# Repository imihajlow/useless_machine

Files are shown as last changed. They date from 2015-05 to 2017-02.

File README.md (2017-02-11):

# Useless machine

This project is an attempt to design a useless machine (the one that does nothing but turing off the switch) from scratch.
The reductor gears are designed to be 3d-printed.
The low-power controller can be reused for other small applications: it provides some GPIO pins, UART, and bidirectional motor driver.
The controller's power consumption is low enough to sustain on a CR2032 battery for more than 1.5 years in standby mode.

* mechanics/ - AutoCAD drawings of the mechanical part of the machine. This folder also contains the belt length calculation script.
* controller/ - the electronic part. Schematic drawing, PCB layout and gerber files for production.
* firmware/ - firmware for the controller. You need SDCC (http://sdcc.sourceforge.net) to compile.

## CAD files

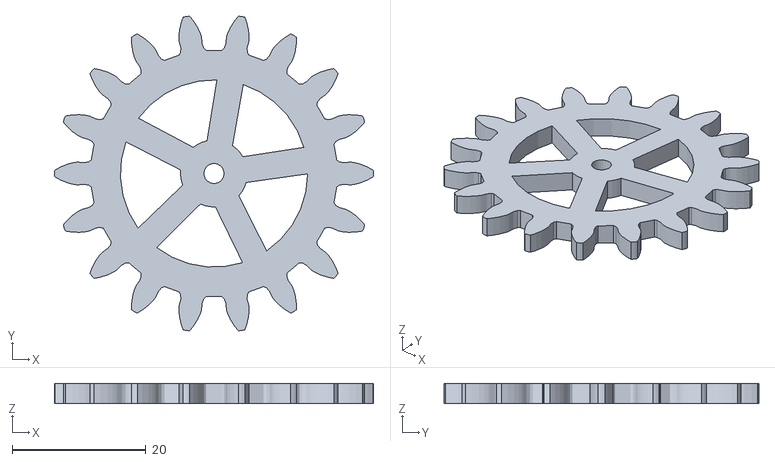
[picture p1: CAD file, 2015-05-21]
mechanics/3.stl
47.7 x 47.1 x 3.00

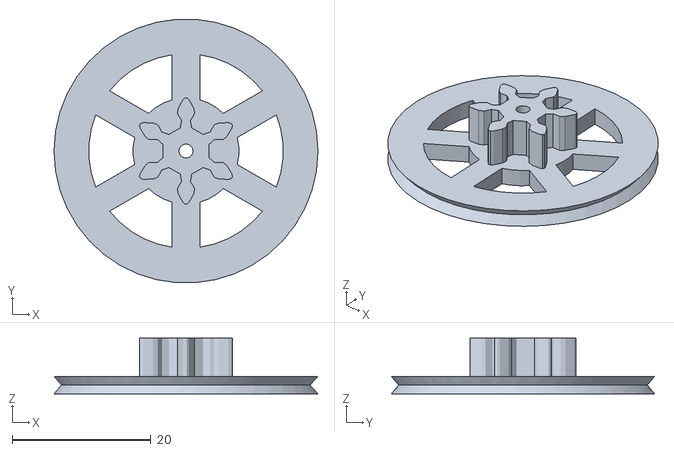
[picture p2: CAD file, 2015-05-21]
mechanics/1.stl
38.0 x 37.9 x 8.00

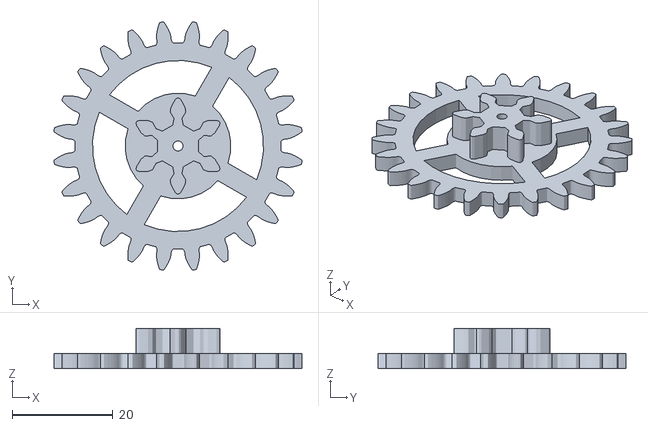
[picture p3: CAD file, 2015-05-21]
mechanics/2.stl
49.3 x 49.3 x 8.00

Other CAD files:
mechanics/layout-v2.dwg
mechanics/ver2.dwg
mechanics/machine.dwg

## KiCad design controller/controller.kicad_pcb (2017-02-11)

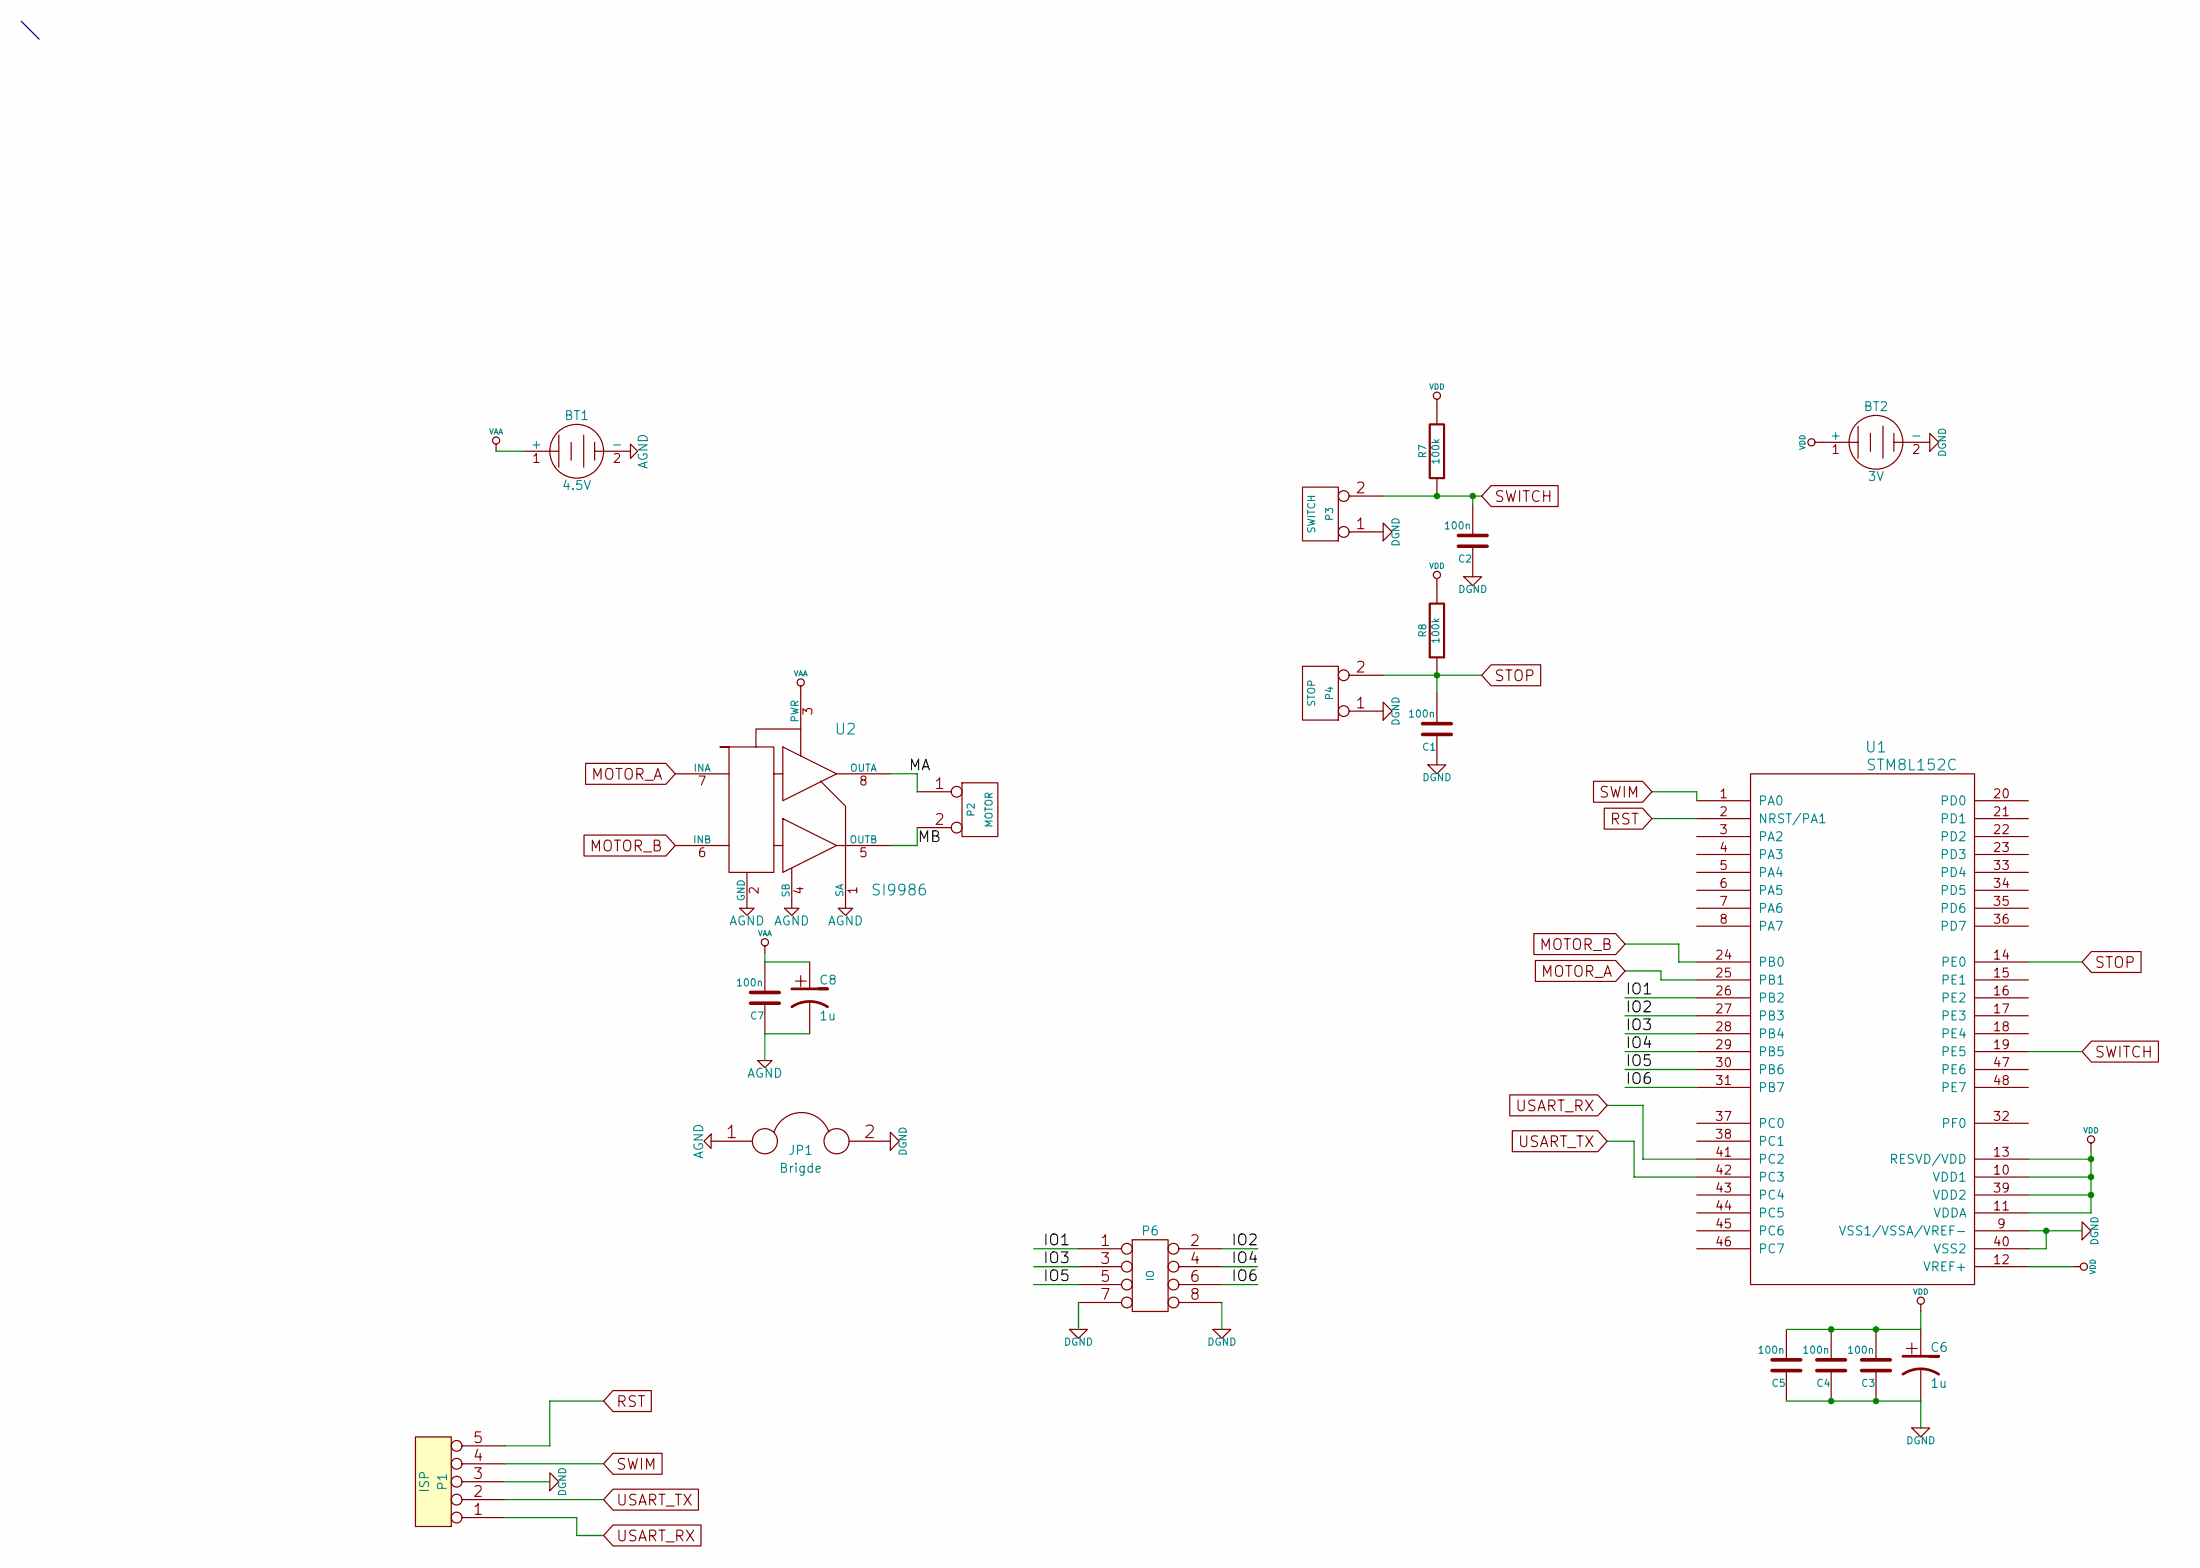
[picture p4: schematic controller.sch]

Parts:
BT1: 4.5V
BT2: 3V
C1, C2, C3, C4, C5, C7: 100n
C6, C8: 1u
JP1: Brigde
P1: ISP
P2: MOTOR
P3: SWITCH
P4: STOP
P6: IO
R7, R8: 100k
U1: STM8L152C
U2: SI9986

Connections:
/IO1: P6.1, U1.26 (PB2)
/IO2: P6.2, U1.27 (PB3)
/IO3: P6.3, U1.28 (PB4)
/IO4: P6.4, U1.29 (PB5)
/IO5: P6.5, U1.30 (PB6)
/IO6: P6.6, U1.31 (PB7)
/MA: P2.1, U2.8 (OUTA)
/MB: P2.2 (PM), U2.5 (OUTB)
AGND: BT1.2 (-), C7.1, C8.2, JP1.1, U2.1 (SA), U2.2 (GND), U2.4 (SB)
DGND: BT2.2 (-), C1.1, C2.1, C3.1, C4.1, C5.1, C6.2, JP1.2, P1.3, P3.1, P4.1, P6.7, P6.8, U1.9 (VSS1/VSSA/VREF-), U1.40 (VSS2)
MOTOR_A: U1.25 (PB1), U2.7 (INA)
MOTOR_B: U1.24 (PB0), U2.6 (INB)
RST: P1.5, U1.2 (NRST/PA1)
STOP: C1.2, P4.2 (PM), R8.1, U1.14 (PE0)
SWIM: P1.4, U1.1 (PA0)
SWITCH: C2.2, P3.2 (PM), R7.1, U1.19 (PE5)
USART_RX: P1.1, U1.41 (PC2)
USART_TX: P1.2, U1.42 (PC3)
VAA: BT1.1 (+), C7.2, C8.1, U2.3 (PWR)
VDD: BT2.1 (+), C3.2, C4.2, C5.2, C6.1, R7.2, R8.2, U1.10 (VDD1), U1.11 (VDDA), U1.12 (VREF+), U1.13 (RESVD/VDD), U1.39 (VDD2)

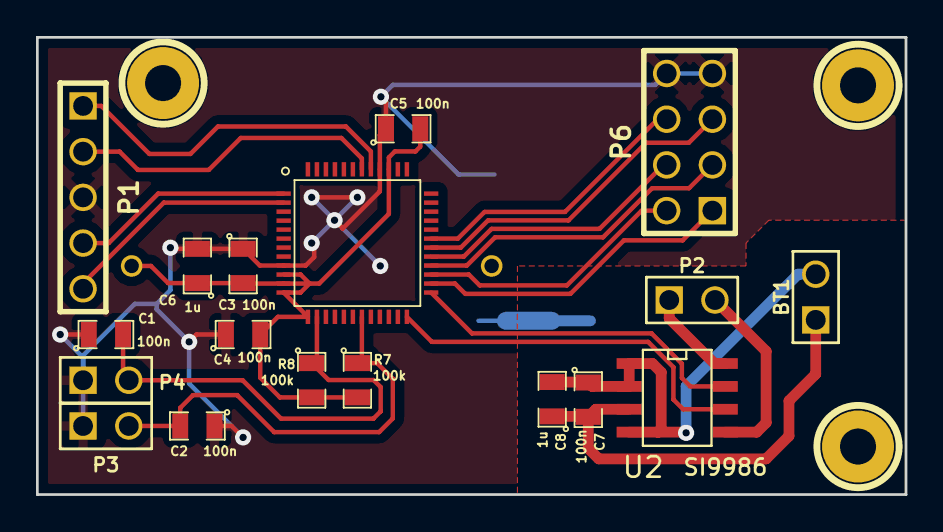
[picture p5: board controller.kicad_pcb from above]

Board: 2 copper layers, 48.3 x 25.4 mm, 19 parts (1 on the bottom side), 20 nets.

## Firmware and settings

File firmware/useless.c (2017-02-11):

#include "stm8l.h"

#define MOTOR_A 2
#define MOTOR_B 1

enum State {
    IDLE,
    WAIT_FORWARD,
    FORWARD,
    WAIT_BACKWARD,
    BACKWARD
};

short getDelayForward(void);
short getDelayBackward(void);

volatile int  irritationCount = 0;

static volatile enum State state = IDLE;

void stopHandler(void);
void switchHandler(void);
void sleepHandler(void);
void setMotor(void);
int getStopState(void);
int getSwitchState(void);
void keepIdleTimer(void);
void disableIdleTimer(void);


void exti0(void) __interrupt(8) {
    // stop
    EXTI_SR1 |= 1 << 0;

    stopHandler();
}

void exti5(void) __interrupt(13) {
    // switch
    EXTI_SR1 |= 1 << 5;

    switchHandler();
}

volatile char firstEvent = 1;
volatile char isSleeping = 0;
void tim1(void) __interrupt(23) {
    if (TIM1_SR1 & TIM_SR1_UIF) {
        if (firstEvent && !isSleeping) { // discard first event
            firstEvent = 0;
        } else {
            isSleeping = 0;
            sleepHandler();
        }
    }

    TIM1_SR1 = 0;
}

void tim3(void) __interrupt(21) {
    TIM3_SR1 = 0;
    disableIdleTimer();
}

void startSleep(unsigned short period) { // units are 10 ms
    if (isSleeping) {
        return; // Already sleeping. ???
    }
    CFG_GCR &= ~CFG_GCR_AL; // disable interrupt-only activation level

    TIM1_ARRH = period >> 8;
    TIM1_ARRL = period & 0xff;

    isSleeping = 1;
    TIM1_CR1 |= TIM_CR1_CEN;
}

int getSwitchState(void) { // 1 is on (need to switch off)
    return (PE_IDR & (1 << 5)) == 0;
}

int getStopState(void) { // 1 is on (pusher is parked)
    return PE_IDR & (1 << 0);
}

void motorForward(void) {
    PB_ODR &= ~MOTOR_A;
    PB_ODR |= MOTOR_B;
}

void motorBackward(void) {
    PB_ODR &= ~MOTOR_B;
    PB_ODR |= MOTOR_A;
}

void motorStop(void) {
    PB_ODR &= ~(MOTOR_A | MOTOR_B);
}

// Set motor according to state
void setMotor(void) {
    switch (state) {
    case FORWARD:
        motorForward();
        break;
    case BACKWARD:
        motorBackward();
        break;
    case IDLE:
    case WAIT_FORWARD:
    case WAIT_BACKWARD:
        motorStop();
        break;
    default:
        motorStop();
        state = IDLE;
        break;
    }
}

void error(void) {
    state = IDLE;
    return;
    //while (1) ;
}

void automata(int justWokeUp) {
    int switchState = getSwitchState(); // 1 is need to switch off
    int stopState = getStopState(); // 1 is parked
    keepIdleTimer();
    switch (state) {
        case IDLE:
            if (switchState) {
                startSleep(getDelayForward());
                state = WAIT_FORWARD;
            }
            break;
        case WAIT_FORWARD:
            if (justWokeUp) {
                if (!switchState) {
                    state = IDLE;
                } else {
                    state = FORWARD;
                }
            } else {
                if (!switchState) {
                    state = IDLE;
                }
            }
            break;
        case FORWARD:
            if (!switchState) {
                startSleep(getDelayBackward());
                state = WAIT_BACKWARD;
                
                //state = BACKWARD;
            }
            break;
        case WAIT_BACKWARD:
            if (justWokeUp) {
                state = BACKWARD;
            } else {
                if (stopState) {
                    state = IDLE;
                } else {
                    state = BACKWARD;
                }
                break;
            }
        case BACKWARD:
            if (stopState) {
                state = IDLE;
            }
            if (switchState) {
                //startSleep(100);
                //state = WAIT_FORWARD;
                state = FORWARD;
            }
            break;
        default:
            state = IDLE;
            break;
    }
    setMotor();
}

void switchHandler(void) {
    if (getSwitchState())
        irritationCount += 1;
    automata(0);
}

void stopHandler(void) {
    automata(0);
}

void sleepHandler() {
    automata(1);
}

#define rim() __asm \
rim \
__endasm

#define halt() __asm \
halt \
__endasm

#define wfi() __asm \
wfi \
__endasm

void setupTimer(void) {
    CLK_PCKENR2 |= 1 << 1; // enable timer clock
    // prescaler is 10000 = 0x2710
    // unit is 10ms
    TIM1_PSCRH = 0x27;
    TIM1_PSCRL = 0x10;


    TIM1_EGR = 1; // generate UE

    TIM1_SR1 = 0; // Reset events

    TIM1_IER = TIM_IER_UIE; // update interrupt enable
    TIM1_CR1 = TIM_CR1_OPM; // up, one pulse
}

volatile char isIdleTimerRunning = 0;
void enableIdleTimer(void) {
    // TIM2 master, TIM3 slave
    CLK_PCKENR1 |= 3; // enable clocks

    // One TIM3 tick in 128*7813 SYSCLK ~ 1s
    TIM2_ARRH = 7813 >> 8;
    TIM2_ARRL = 7813 & 0xff;

    TIM2_PSCR = 7;

    // Update
    TIM2_EGR = 1; // generate UE
    TIM2_SR1 = 0; // Reset events

    TIM3_IER = TIM_IER_UIE;

    // 1. Configure timer A in master mode so
    // that it outputs a periodic trigger signal on each UEV.
    // To configure that a rising edge is output on TRGO1
    // each time an update event is generated,
    // write MMS = 010 in the TIMx_CR2 register.
    TIM2_CR2 = TIM_CR2_MMS(2);

    // 2. Connect the TRGO1 output of timer A to timer B,
    // timer B must be configured in slave mode
    // using ITR1 as the internal trigger.
    // Select this through the TS bits in the TIMx_SMCR register.

    // 3. Put the clock/trigger controller in external clock mode 1,
    // by writing SMS = 111 in the TIMx_SMCR register.
    // This causes timer B to be clocked by the rising edge
    // of the periodic timer A trigger signal
    // (which corresponds to the timer A counter overflow).
    TIM3_SMCR = TIM_SMCR_MSM | TIM_SMCR_TS(3) | TIM_SMCR_SMS(7);
    
    // 4. Enable both timers by setting their respective CEN bits (TIMx_CR1 register).

    TIM3_ARRH = 0;
    TIM3_ARRL = 60; // 60 s period

    TIM3_CR1 |= TIM_CR1_OPM;

    TIM2_CR1 |= TIM_CR1_CEN;
    TIM3_CR1 |= TIM_CR1_CEN;
    isIdleTimerRunning = 1;
    CFG_GCR &= ~CFG_GCR_AL; // normal activation level

}

void keepIdleTimer(void) {
    if (!isIdleTimerRunning)
        enableIdleTimer();
    TIM3_IER = 0;
    TIM3_CNTRH = 0;
    TIM3_CNTRL = 0;
    TIM2_CNTRH = 0;
    TIM2_CNTRL = 0;
    TIM3_SR1 = 0;
    TIM3_IER = TIM_IER_UIE;
}

void disableIdleTimer(void) {
    TIM2_CR1 &= ~TIM_CR1_CEN;
    TIM3_CR1 &= ~TIM_CR1_CEN;

    CLK_PCKENR1 &= ~3; // disable clocks
    isIdleTimerRunning = 0;
    irritationCount = 0;
}

short getDelayForward(void) {
    if (irritationCount < 3) {
        return 100;
    } else if (irritationCount < 10) {
        return 10;
    } else {
        return 1000;
    }
}

short getDelayBackward(void) {
    if (irritationCount < 3) {
        return 10;
    } else if (irritationCount < 10) {
        return 200;
    } else if (irritationCount < 20) {
        return 10;
    } else {
        return 1000;
    }
}

int main(void) {
    CLK_PCKENR2 = 0; // disable boot ROM clock

    // Set all ports to pull-up
    // input and no interrupt by default
    PA_CR1 = 0xFF; // pull-up
    PB_CR1 = 0xFF; // pull-up
    PC_CR1 = 0xFF; // pull-up
    PD_CR1 = 0xFF; // pull-up
    PE_CR1 = 0xFF; // pull-up
    PF_CR1 = 0x01; // pull-up

    // Configure motor pins
    PB_DDR |= MOTOR_A | MOTOR_B; // output
    // already push-pull (CR1 = 1)
    // normal mode by default

    // Configure input pins
    // input by default
    PE_CR2 |= (1 << 0) | (1 << 5); // interrupt
    // already pull-up

    EXTI_CR1 = (3) << 0; // any edge on bit 0
    EXTI_CR2 = (3) << 2; // any edge on bit 5

    state = IDLE;
    setupTimer();
    automata(0);
    rim(); // enable interrupts
    while (1) {
        if (isSleeping || isIdleTimerRunning) {
            wfi();
        } else {
            CFG_GCR |= CFG_GCR_AL; // interrupt-only activation level
            halt();
        }
    }
    return 0;
}

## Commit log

2017-02-11 Moved mechanics drawings into a separate folder
    [1.stl, 2.stl, 3.stl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]
2017-02-11 Removed outdated drawings
    [motor.dwg, shaft.dwg]
2017-02-11 Controller schemantic and PCB files added
    [controller.kicad_pcb, controller.sch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]
2017-02-11 Moved belt calculation script
2017-02-21 Added SVG layout of the box to be used by laser cutter.
